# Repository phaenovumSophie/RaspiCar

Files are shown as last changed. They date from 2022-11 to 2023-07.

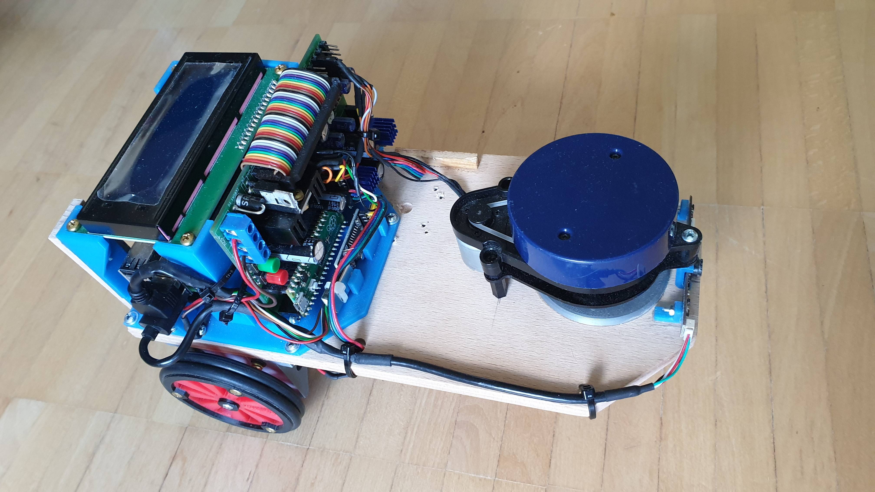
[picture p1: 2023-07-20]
RaspiCar_v2.jpg

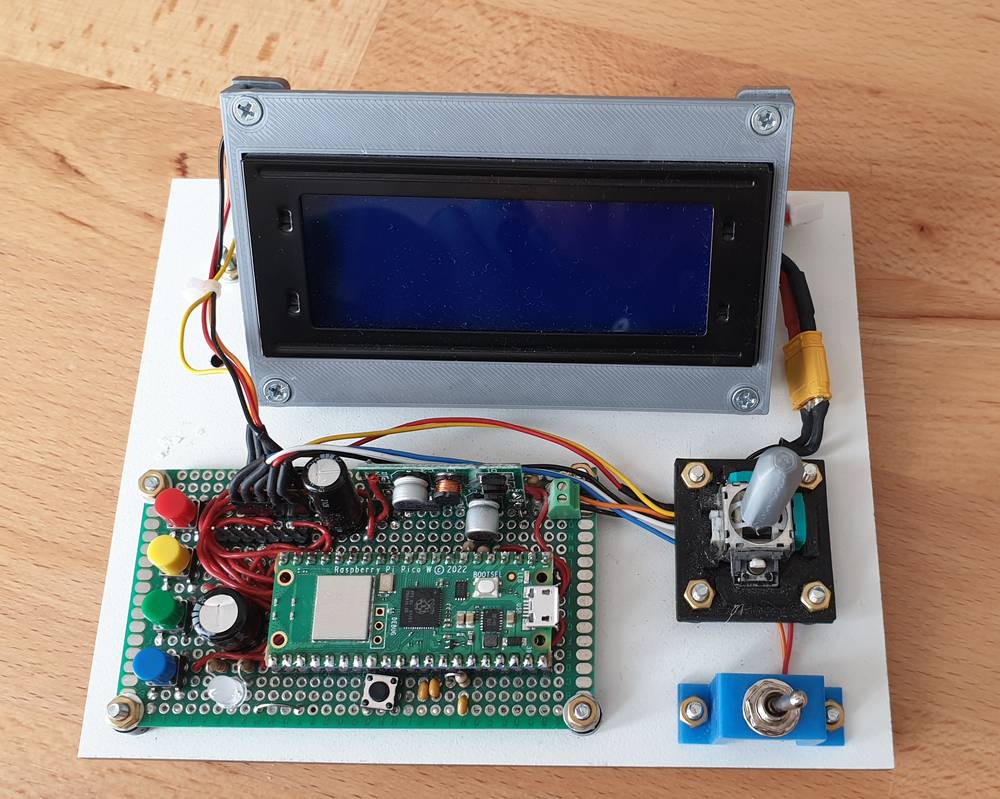
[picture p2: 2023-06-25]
RaspiCar-Controller/Circuit/Controller-Foto.jpg

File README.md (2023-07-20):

# RaspiCar
A model car equipped with a Raspberry Pi, intended for experimenting with tools and algorithms for autonomous navigation

This is a simple platform for experimenting. At this stage clearly work in progress ...

The car is based on two stepper motors for the left and right driving wheel. In addition there is a free spinning wheel in the front. Driving direction is controlled by different speed settings for the motors. The car is capable of turning on the spot. Power is provided a by a LiPo battery of 3 cells.

Raspberry Pi:
=============
The Raspberry Pi provides navigation and overall management of the car. The navigations is based on the various sensors. The software is written primarily in Python. Prototype software is avaiable to support ultrasonic sensors, LiDAR, camera and a NRF24 module for remote control. There are also experiments with machine learning alogrithms (SciKit Learn). More to be developed and to follow.

Python files:
- io_ctrl.py - This module defines the I/Os for the Raspberry Pi and a tool to send commands to the motor driver via a serial interface
- much more to come ...

Motor Driver:
=============
In addition to the Raspberry Pi, there is a board comprising a 5V step down converter, a rp2040 microcontroller, a LCD and adapters for various devices such as LiDAR, distance sensors and more. The rp2040 generates the step and direction signals for the stepper motors, with this releasing the real time workload from the Raspberry Pi. The rp2040 interfaces with the Raspberry Pi via a serial interface running at115200 baud. The rp2040 also takes care of power management by raising a shutdown signal in case the battery voltage is running low. The software for the rp2040 is based on Arduino/C++

Arduino files for the motor driver:
- rp2040_motor_driver.ino: main program
- motors.cpp, motors.h: class to run the stepper motors
- display.cpp, display.h: class to run the display
- battery.cpp, battery.h: class to provide battery and power management

List of motor commands:
The Raspberry Pi sends commands via the serial interface and receives responses. This can easily by tested via a standard terminal tool (e.g. PUTTY).
- ME0,0 / ME1,1  - disables or enables motor A and B
- MP0,0 / MP1,1  - switches motor A and B on or off
- MD0,0 / MD1,1  - sets the direction of the motor (1 -> forward, 0 -> backward)
- MR<l>,<r> - sets the speed of the motors in rounds per minute. The range is 0 to 1500. Example: "MR200,500"
- DC - clears the display (title and message)
- DT - prints a title of up to 0 characters on line 1 of the display (maximum 20 characters)
- DM - prints a message of up to 40 character on line 2 and 3 of the display
- BV - returns the current battery voltage
- BS - returns the battery voltage and the system status, separated by comma 

List of system status:
  - 0 - STATUS_OK                   'OK' - all fine
  - 1 - STATUS_BAT_LOW              'BL' - Battery low, voltage below 10.5V
  - 2 - STATUS_BAT_SHUTDOWN         'BS' - Battery very low, shutdown requested due to low power, waiting for Raspi to respond
  - 3 - STATUS_BAT_EXTERNAL         'BE  - System running on 5V external power
  - 4 - STATUS_SHUTDOWN_REQUESTED   'SR' - Shutdwon requested by user, waiting for Raspi to respond
  - 5 - STATUS_SHUTDOWN_ACTIVE      'SX' - Shutdown in progress, power will be shut in less than 10 secs

SLW October 2022

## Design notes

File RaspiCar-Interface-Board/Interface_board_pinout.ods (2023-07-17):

Raspi Pin | Raspi GPIO | Function | Connector | Pin
2 | - | +5V Power | J8 Raspi I2C | 2
3 | 02 | I2C SDA | J8 Raspi I2C | 3
4 | - | +5V Power | J8 Raspi I2C | 2
5 | 03 | I2C SCL | J8 Raspi I2C | 4
6 | - | GND | - | -
9 | - | GND | - | -
10 | 15 | Raspi RxD | J6 LiDAR | 3
14 | - | GND | - | -
17 | 3.3V Out | SPI Vcc | J5 Raspi SPI | 2
19 | 10 | Raspi MOSI | J5 Raspi SPI | 4
20 | - | GND | - | -
21 | 09 | Raspi MISO | J5 Raspi SPI | 5
23 | 11 | Raspi SCLK | J5 Raspi SPI | 3
24 | 08 | Raspi CE | J5 Raspi SPI | 6
25 | - | GND | - | -
29 | 05 | Raspi IN | Pico GP2 | 4
30 | - | GND | - | -
31 | 06 | Dual LED red | - | -
33 | '13 | Dual LED green | - | -
34 | - | GND | - | -
35 | 19 | Raspi OUT | Pico GP3 | 5
37 | 26 | LED green | - | -
39 | - | GND | - | -
40 | '21 | LiDAR Power | J6 LiDAR | 2

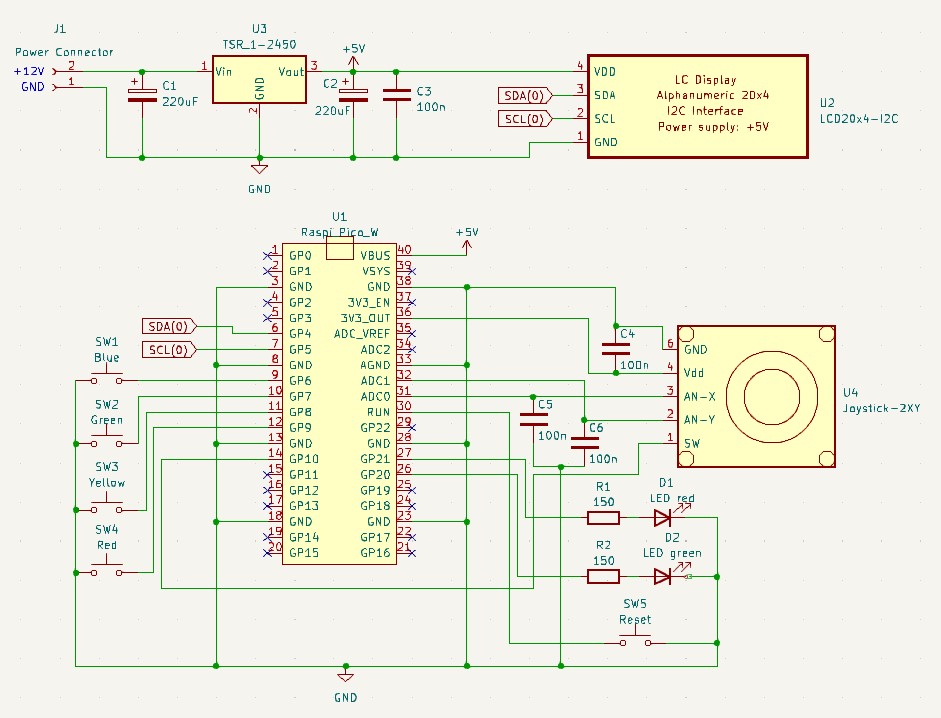
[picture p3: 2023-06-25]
RaspiCar-Controller/Circuit/Schaltplan.jpg

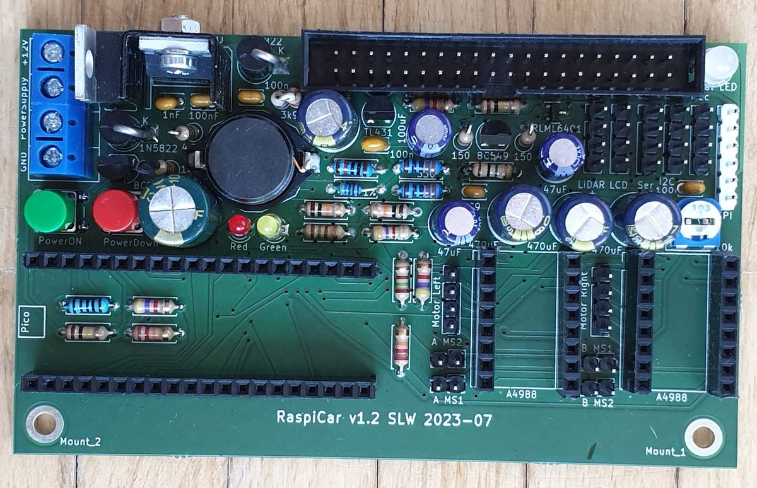
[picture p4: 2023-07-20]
RaspiCar-Interface-Board/Foto.jpg

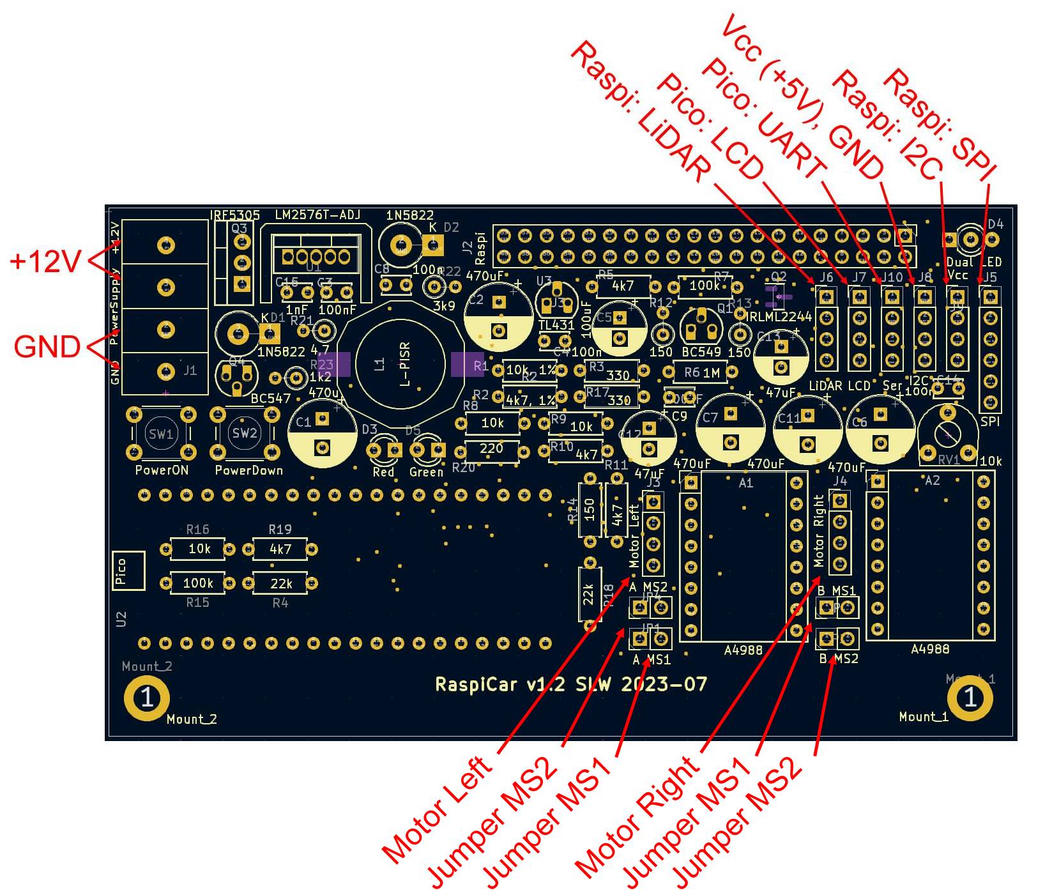
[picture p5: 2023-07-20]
RaspiCar-Interface-Board/RaspiCar-PCB-v1.2.jpg

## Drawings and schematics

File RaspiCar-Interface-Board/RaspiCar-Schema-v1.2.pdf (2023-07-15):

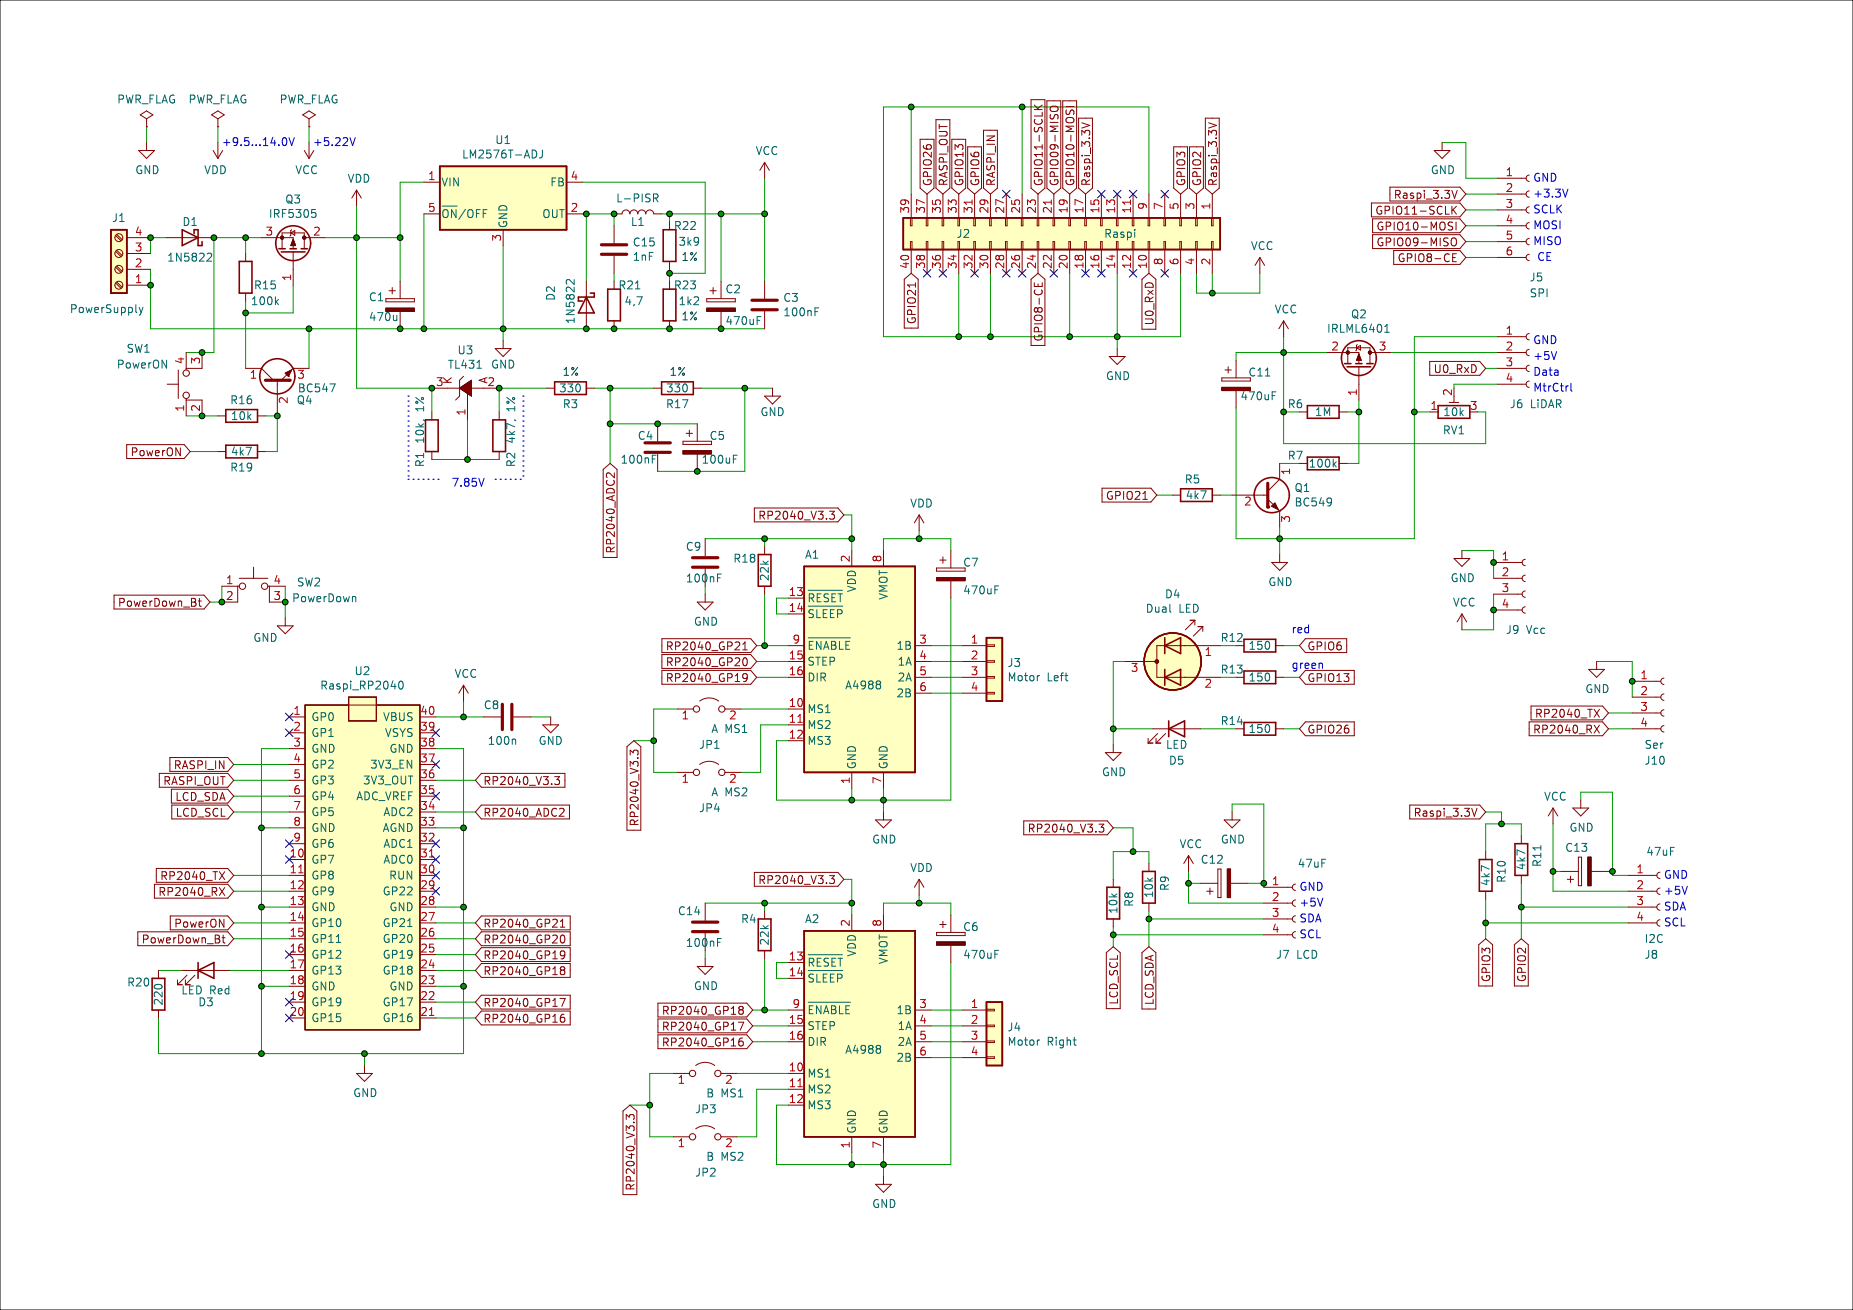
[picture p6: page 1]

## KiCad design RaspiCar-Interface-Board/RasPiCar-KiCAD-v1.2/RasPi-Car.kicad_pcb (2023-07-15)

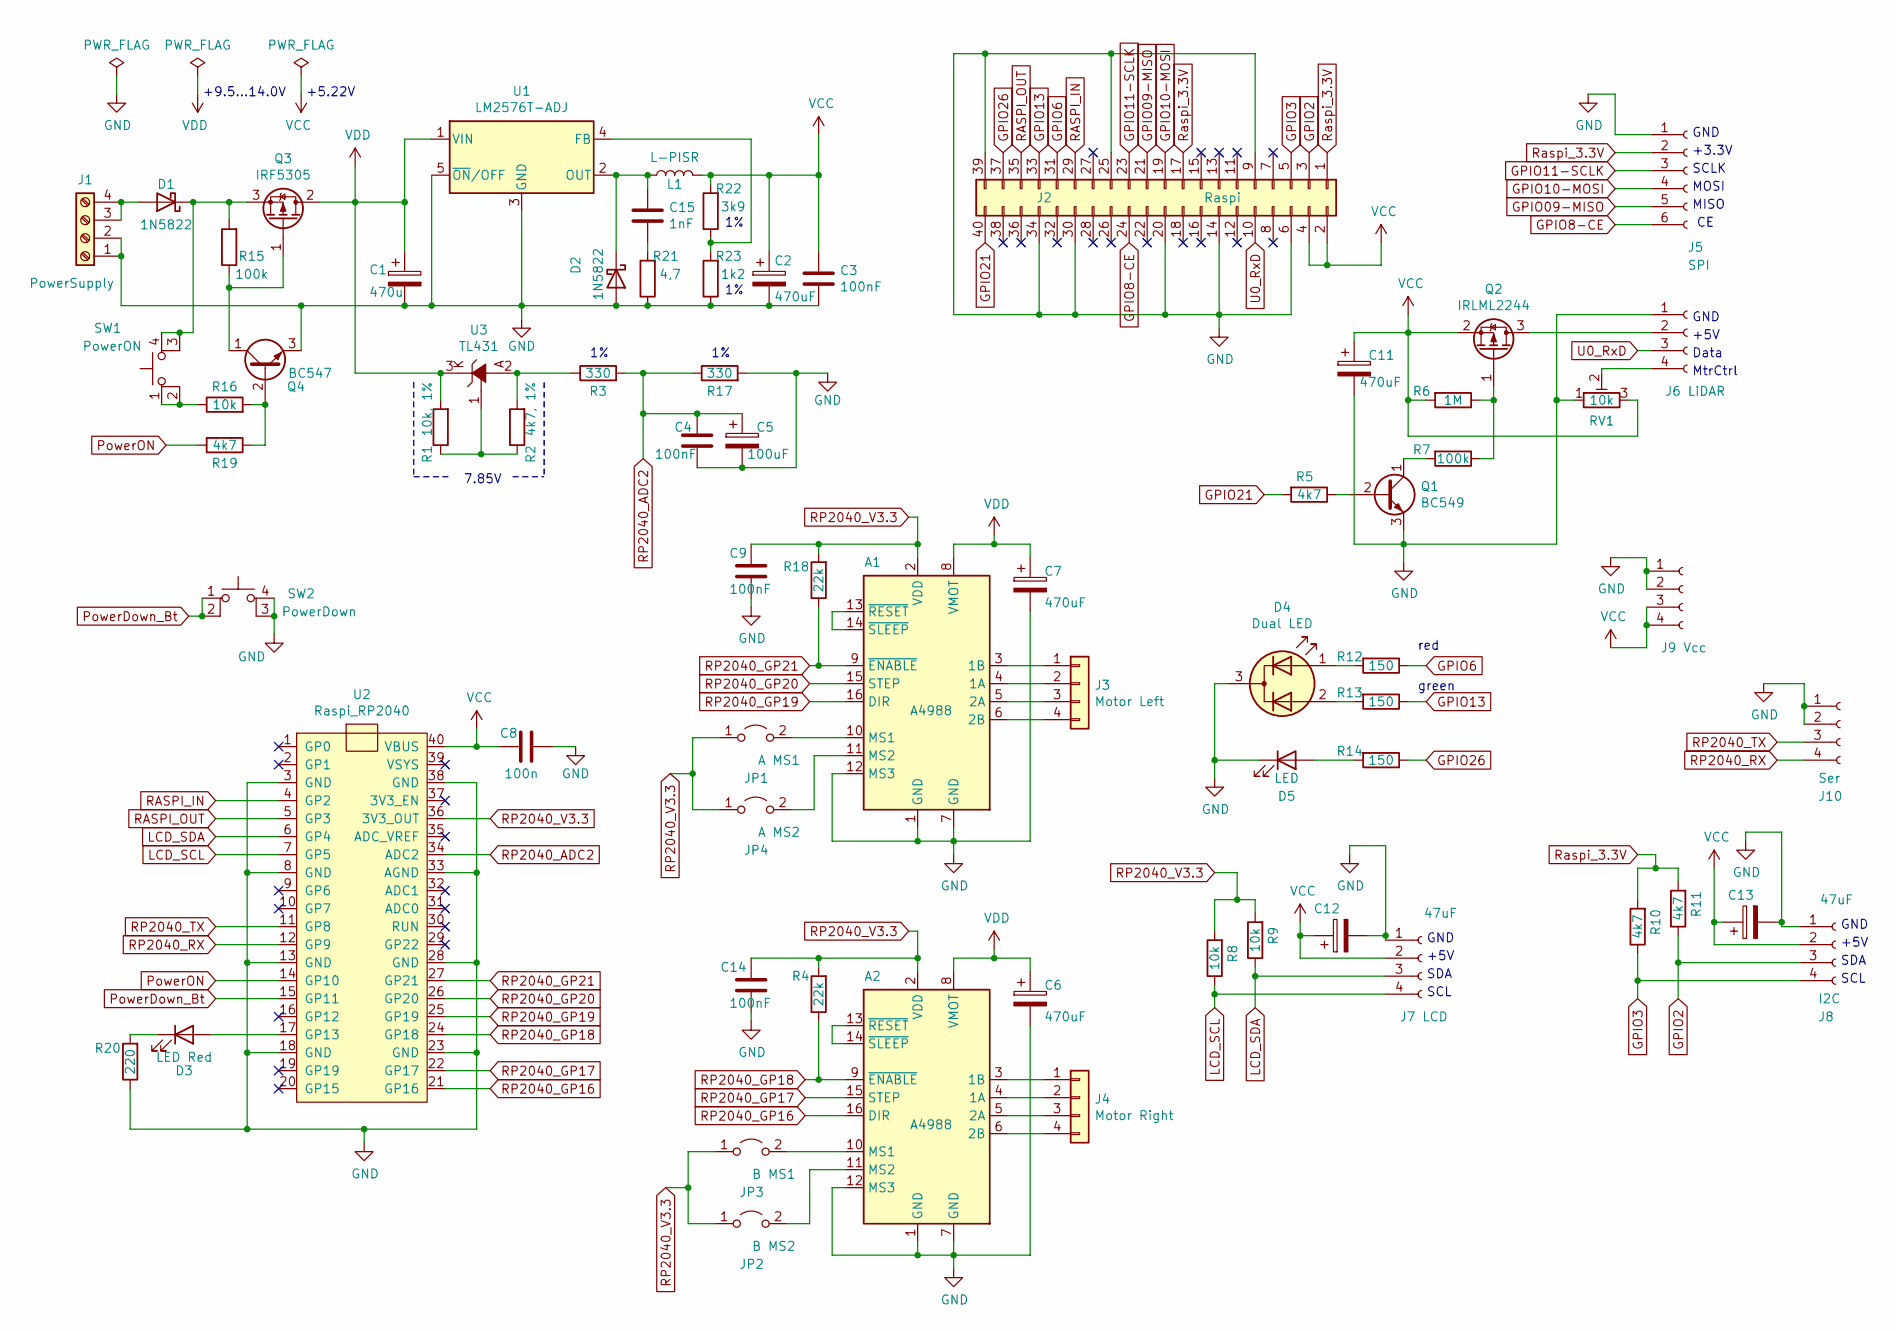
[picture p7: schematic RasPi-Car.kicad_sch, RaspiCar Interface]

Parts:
A1, A2: A4988; Pololu_Breakout-16_15.2x20.3mm
C1: 470u; CP_Radial_D8.0mm_P3.50mm
C2, C6, C7, C11: 470uF; CP_Radial_D8.0mm_P3.50mm
C3, C4, C9, C14: 100nF; C_Disc_D3.4mm_W2.1mm_P2.50mm
C5: 100uF; CP_Radial_D6.3mm_P2.50mm
C8: 100n; C_Disc_D3.4mm_W2.1mm_P2.50mm
C12, C13: 47uF; CP_Radial_D6.3mm_P2.50mm
C15: 1nF; C_Disc_D3.4mm_W2.1mm_P2.50mm
D1, D2: 1N5822; D_DO-201AE_P3.81mm_Vertical_KathodeUp
D3: LED Red; LED_D3.0mm
D4: Dual LED; LED_D3.0mm-3-center-kathode
D5: LED; LED_D3.0mm
J1: PowerSupply; ScrewTerminal_1x4
J2: Raspi; PinHeader_2x20_P2.54mm_Vertical
J3: Motor Left; PinHeader_1x04_P2.54mm_Vertical
J4: Motor Right; PinHeader_1x04_P2.54mm_Vertical
J5: SPI; PinHeader_1x06_P2.54mm_Vertical
J6: LiDAR; PinHeader_1x04_P2.54mm_Vertical
J7: LCD; PinHeader_1x04_P2.54mm_Vertical
J8: I2C; PinHeader_1x04_P2.54mm_Vertical
J9: Vcc; PinHeader_1x04_P2.54mm_Vertical
J10: Ser; PinHeader_1x04_P2.54mm_Vertical
JP1: A MS1; PinHeader_1x02_P2.54mm_Vertical
JP2: B MS2; PinHeader_1x02_P2.54mm_Vertical
JP3: B MS1; PinHeader_1x02_P2.54mm_Vertical
JP4: A MS2; PinHeader_1x02_P2.54mm_Vertical
L1: L-PISR; L-PISR-100
Q1: BC549; TO-92_HandSolder
Q2: IRLML2244; SOT-23
Q3: IRF5305; TO-220-3_Vertical
Q4: BC547; TO-92_HandSolder
R1: 10k, 1%; R_Axial_DIN0207_L6.3mm_D2.5mm_P7.62mm_Horizontal
R2: 4k7, 1%; R_Axial_DIN0207_L6.3mm_D2.5mm_P7.62mm_Horizontal
R3, R17: 330; R_Axial_DIN0207_L6.3mm_D2.5mm_P7.62mm_Horizontal
R4, R18: 22k; R_Axial_DIN0207_L6.3mm_D2.5mm_P7.62mm_Horizontal
R5, R10, R11, R19: 4k7; R_Axial_DIN0207_L6.3mm_D2.5mm_P7.62mm_Horizontal
R6: 1M; R_Axial_DIN0207_L6.3mm_D2.5mm_P7.62mm_Horizontal
R7, R15: 100k; R_Axial_DIN0207_L6.3mm_D2.5mm_P7.62mm_Horizontal
R8, R9, R16: 10k; R_Axial_DIN0207_L6.3mm_D2.5mm_P7.62mm_Horizontal
R12, R13: 150; R_Axial_DIN0207_L6.3mm_D2.5mm_P2.54mm_Vertical
R14: 150; R_Axial_DIN0207_L6.3mm_D2.5mm_P7.62mm_Horizontal
R20: 220; R_Axial_DIN0207_L6.3mm_D2.5mm_P7.62mm_Horizontal
R21: 4,7; R_Axial_DIN0207_L6.3mm_D2.5mm_P2.54mm_Vertical
R22: 3k9; R_Axial_DIN0207_L6.3mm_D2.5mm_P2.54mm_Vertical
R23: 1k2; R_Axial_DIN0207_L6.3mm_D2.5mm_P2.54mm_Vertical
RV1: 10k; R-Trim_horizontal
SW1: PowerON; SW_PUSH_6mm_H5mm
SW2: PowerDown; SW_PUSH_6mm_H5mm
U1: LM2576T-ADJ; TO-220-5_Vertical_tiny_heatsink
U2: Raspi_RP2040
U3: TL431; TO-92_HandSolder

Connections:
GND: A1.1 (GND), A1.7 (GND), A1.12 (MS3), A2.1 (GND), A2.7 (GND), A2.12 (MS3), C1.2, C2.2, C3.2, C4.1, C5.2, C6.2, C7.2, C8.1, C9.2, C11.2, C12.2, C13.2, C14.2, D2.2 (A), D4.3 (K), D5.1 (K), J1.1, J1.2, J2.6, J2.9, J2.14, J2.20, J2.25, J2.30, J2.34, J2.39, J5.1, J6.1, J7.1, J8.1, J9.1, J9.2, J10.1, J10.2, Q1.3 (E), Q4.3 (E), R17.2, R20.1, R21.1, R23.1, RV1.1, SW2.3 (K), SW2.4 (A), U1.3 (GND), U1.5 (~ON/OFF), U2.3 (GND), U2.8 (GND), U2.13 (GND), U2.18 (GND), U2.23 (GND), U2.28 (GND), U2.33 (AGND), U2.38 (GND)
GPIO2: J2.3, J8.3, R11.1
GPIO3: J2.5, J8.4, R10.1
GPIO6: J2.31, R12.1
GPIO8-CE: J2.24, J5.6
GPIO09-MISO: J2.21, J5.5
GPIO10-MOSI: J2.19, J5.4
GPIO11-SCLK: J2.23, J5.3
GPIO13: J2.33, R13.1
GPIO21: J2.40, R5.2
GPIO26: J2.37, R14.1
LCD_SCL: J7.4, R8.1, U2.7 (GP5)
LCD_SDA: J7.3, R9.1, U2.6 (GP4)
unnamed: A1.4 (1A), J3.2
unnamed: A1.3 (1B), J3.1
unnamed: A1.5 (2A), J3.3
unnamed: A1.6 (2B), J3.4
unnamed: A1.10 (MS1), JP1.2 (B)
unnamed: A1.11 (MS2), JP4.2 (B)
unnamed: A1.13 (~RESET), A1.14 (~SLEEP)
unnamed: A2.4 (1A), J4.2
unnamed: A2.3 (1B), J4.1
unnamed: A2.5 (2A), J4.3
unnamed: A2.6 (2B), J4.4
unnamed: A2.10 (MS1), JP3.2 (B)
unnamed: A2.11 (MS2), JP2.2 (B)
unnamed: A2.13 (~RESET), A2.14 (~SLEEP)
unnamed: C15.2, R21.2
unnamed: D1.2 (A), J1.3, J1.4
unnamed: D1.1 (K), Q3.3 (S), R15.2, SW1.3 (K), SW1.4 (A)
unnamed: C15.1, D2.1 (K), L1.1, U1.2 (OUT)
unnamed: D3.2 (A), U2.17 (GP13)
unnamed: D3.1 (K), R20.2
unnamed: D4.1 (A1), R12.2
unnamed: D4.2 (A2), R13.2
unnamed: D5.2 (A), R14.2
unnamed: J6.2, Q2.3 (D)
unnamed: J6.4, RV1.2
unnamed: Q1.2 (B), R5.1
unnamed: Q1.1 (C), R7.2
unnamed: Q2.1 (G), R6.1, R7.1
unnamed: Q3.1 (G), Q4.1 (C), R15.1
unnamed: Q4.2 (B), R16.2, R19.1
unnamed: R16.1, SW1.1, SW1.2
unnamed: R22.1, R23.2, U1.4 (FB)
unnamed: R2.2, R3.1, U3.2 (A)
unnamed: R1.1, R2.1, U3.1 (R)
PowerDown_Bt: SW2.1, SW2.2, U2.15 (GP11)
PowerON: R19.2, U2.14 (GP10)
RASPI_IN: J2.29, U2.4 (GP2)
RASPI_OUT: J2.35, U2.5 (GP3)
RP2040_ADC2: C4.2, C5.1, R3.2, R17.1, U2.34 (ADC2)
RP2040_GP16: A2.16 (DIR), U2.21 (GP16)
RP2040_GP17: A2.15 (STEP), U2.22 (GP17)
RP2040_GP18: A2.9 (~ENABLE), R4.1, U2.24 (GP18)
RP2040_GP19: A1.16 (DIR), U2.25 (GP19)
RP2040_GP20: A1.15 (STEP), U2.26 (GP20)
RP2040_GP21: A1.9 (~ENABLE), R18.1, U2.27 (GP21)
RP2040_RX: J10.4, U2.12 (GP9)
RP2040_TX: J10.3, U2.11 (GP8)
RP2040_V3.3: A1.2 (VDD), A2.2 (VDD), C9.1, C14.1, JP1.1 (A), JP2.1 (A), JP3.1 (A), JP4.1 (A), R4.2, R8.2, R9.2, R18.2, U2.36 (3V3_OUT)
Raspi_3.3V: J2.1, J2.17, J5.2, R10.2, R11.2
U0_RxD: J2.10, J6.3
VCC: C2.1, C3.1, C8.2, C11.1, C12.1, C13.1, J2.2, J2.4, J7.2, J8.2, J9.3, J9.4, L1.2, Q2.2 (S), R6.2, R22.2, RV1.3, U2.40 (VBUS)
VDD: A1.8 (VMOT), A2.8 (VMOT), C1.1, C6.1, C7.1, Q3.2 (D), R1.2, U1.1 (VIN), U3.3 (K)

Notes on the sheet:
SCL
+9.5...14.0V
+5V
7.85V
SDA
MtrCtrl
Data
SCLK
red
MISO
GND
+5.22V
+3.3V
MOSI
green

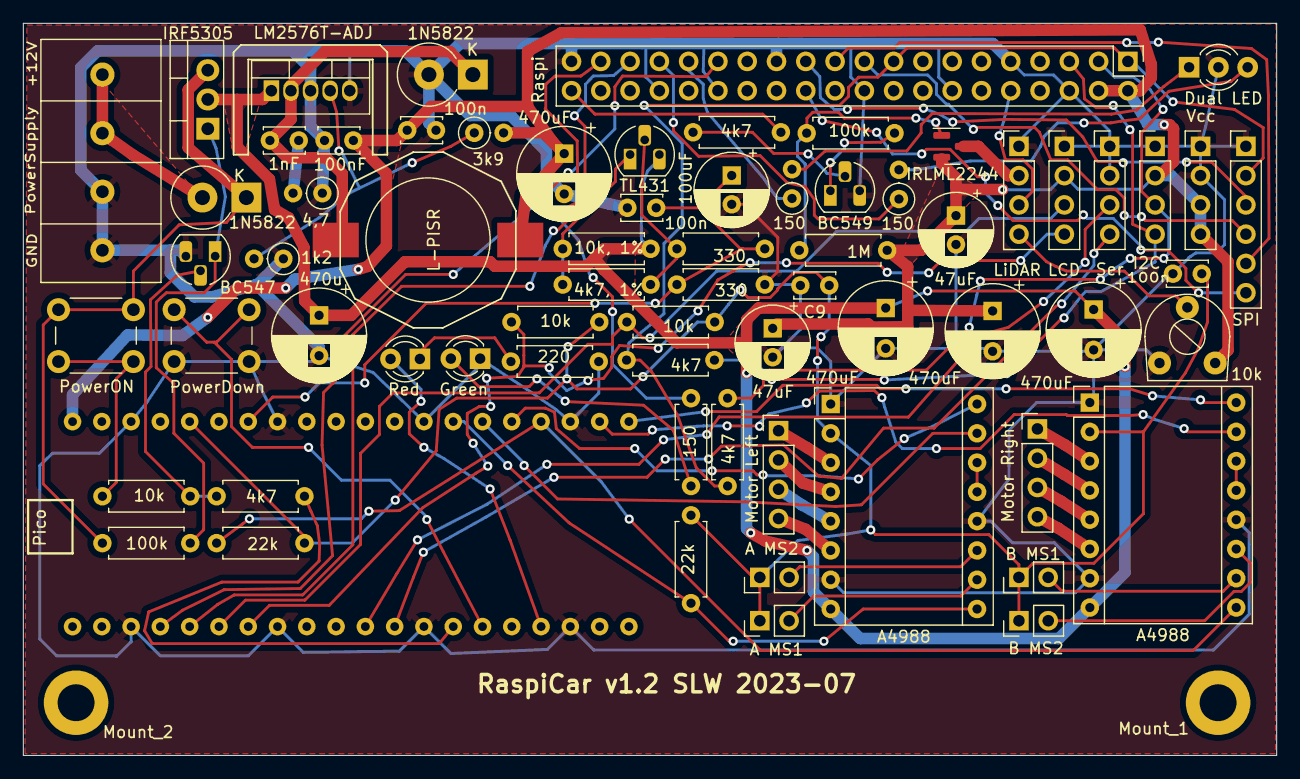
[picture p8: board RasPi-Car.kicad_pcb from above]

Board: 2 copper layers, 108.7 x 63.5 mm, 71 parts (0 on the bottom side), 65 nets.

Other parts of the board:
Mount_1: Mount_1; MountingHole_3.2mm_M3_DIN965_Pad
Mount_2: Mount_2; MountingHole_3.2mm_M3_DIN965_Pad

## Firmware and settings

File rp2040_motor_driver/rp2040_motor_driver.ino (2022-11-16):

/*
 * rp2040 Motor Driver (RaspiCar)
 * This module is part of the phaenovum RaspiCar project. 
 * It provides driver function for two stepper motors. Beyond that, it serves 
 * as power and battery manager. Finally, it includes a LCD display to shows 
 * status information and simplify debugging. It uses a seruial interface
 * (fixed baud rate at 115200) for communication with the Raspberry Pi. 
 * 
 * SLW - October 2022
 */

#include "display.h"
#include "motors.h"
#include "battery.h"
#include "util.h"

#define BUF_SIZE 40

// Pins
#define SERIAL_TX         8      // serial interface to Raspberry Pi
#define SERIAL_RX         9
#define RASPI_IN          2      // reserve: additional GPIO to RaspiPi 
#define RASPI_OUT         3      // reserve: additional GPIO to RaspiPi 

// Decode input from serial interface
#define VALID_LIMIT 999999

// Global variables
LCD_Display display;
Motors motors;
Battery bat;
char buf[BUF_SIZE];
int buf_pnt=0;
int i = 0;
volatile uint8_t job_flags = 0b00000000;
int power_down_bt_status = 0;


//-------------------------------------------------------------------------
// Adds a char from the serial interface to the input buffer. 
// Returns false, unless a end-of-line character is detected.
bool add_to_buffer(char c) {
  switch ((uint8_t) c) {
    case 13:   // carriage return
    case 10:   // line feed
      buf[buf_pnt] = '\0';
      buf_pnt = 0;
      return true;
    case 8:    // backspace
      buf[buf_pnt] = '\0';
      if (buf_pnt > 0) buf_pnt -= 1;
      break;
    default:     // all other chars
      buf[buf_pnt] = c;
      if (buf_pnt < BUF_SIZE - 1) 
      ++buf_pnt;
  }
  return false;
}

//-------------------------------------------------------------------------
// get_int
// Extracts an integer from the input buffer. 
// Moves the pointer to the next position after the integer
int32_t get_int(uint8_t *pnt) {
  int32_t result = 0;
  bool negative_flag = false, done = false, valid = false;

  while (buf[*pnt] == ' ') *pnt += 1;     // skip leading blanks
  
  while (!done) {
    if (buf[*pnt] == '+') {
      negative_flag = false;
    } else if (buf[*pnt] == '-') {
      negative_flag = true;
    } else if ((buf[*pnt] >= '0') && (buf[*pnt] <= '9')) {
      result = result * 10;
      result += buf[*pnt] - '0';
      valid = true;
    } else {
      done = true;
    }
    if (buf[*pnt] != '\0')      // don't progress beyond end of string
      *pnt += 1;
  }
  if (!valid) {
    result = VALID_LIMIT;
  } else if (negative_flag) {
    result = -result;
  }
  return result;
}

//-------------------------------------------------------------------------
void decode_bat_command(uint8_t pnt) {
  char local_buf[16];
  bool okay = true;
  
  switch (buf[pnt]) {
    case 'v':               // get battery voltage
    case 'V':
      itoaf(bat.get_voltage(), local_buf, 4, 2, false);
      uart_puts(uart1, local_buf); 
      break;

    case 's':               // get battery status
    case 'S':
      bat.get_full_status(local_buf);
      uart_puts(uart1, local_buf);
      break;

    case 'x':
    case 'X':
      display.print_msg("Shutting down");
      bat.start_shutdown();
      uart_puts(uart1, "OK");
      break;
 
    default:
      okay = false;
  }
  if (!okay) {
      uart_puts(uart1, "Battery command not recognized: ");
      uart_puts(uart1, buf);
  }
  uart_puts(uart1, "\r\n");
}

//-------------------------------------------------------------------------
void decode_display_command(uint8_t pnt) {
  bool okay = true;
  
  switch (buf[pnt]) {
    case 'c':           // clear display
    case 'C':
      display.clear();
      break;
      
    case 't':           // print title
    case 'T':
      display.print_title(buf+2);
      break;
      
    case 'm':           // print message
    case 'M':
      display.print_msg(buf+2);
      break;
      
    default:
      okay = false;
  }
  if (okay) {
    uart_puts(uart1, "OK");
  } else {
      uart_puts(uart1, "Display command not recognized: ");
      uart_puts(uart1, buf);
  }
  uart_puts(uart1, "\r\n");
}

//-------------------------------------------------------------------------
void decode_motor_command(uint8_t pnt) {
  int32_t a, b;
  bool okay = true;

  switch (buf[pnt]) {
    case 'd':
    case 'D':                                 // dir
      pnt += 1;
      a = get_int(&pnt);    
      b = get_int(&pnt);
      if (a < VALID_LIMIT) {
        motors.set_a_dir(a > 0);
      }
      if (b < VALID_LIMIT) {
        motors.set_b_dir(b > 0);
      }     
      break;
    
    case 'e':
    case 'E':                                 // enable
      pnt += 1;
      a = get_int(&pnt);    
      b = get_int(&pnt);
      if (a < VALID_LIMIT) {
        motors.set_a_enable(a > 0);
        display.mot_a_enabled(motors.get_a_enabled());
      }
      if (b < VALID_LIMIT) {
        motors.set_b_enable(b > 0);
        display.mot_b_enabled(motors.get_b_enabled());
      }     
      break;
      
    case 'p':
    case 'P':                                 // power
      pnt += 1;
      a = get_int(&pnt);    
      b = get_int(&pnt);
      if (a < VALID_LIMIT) {
        motors.set_a_power(a > 0);
        display.mot_a_power(motors.get_a_power());
      }
      if (b < VALID_LIMIT) {
        motors.set_b_power(b > 0);
        display.mot_b_power(motors.get_b_power());
      }     
      break;

    /*
    case 't':                             // set cycle time
    case 'T':
      pnt += 1;
      a = get_int(&pnt);    
      b = get_int(&pnt);
      if (a < VALID_LIMIT) {
        if (a < MOT_STEP_TIME_MIN) {
          a = MOT_STEP_TIME_MIN;
          uart_puts(uart1, "Mot A: Lower limit\n\r");
        }
        else if (a > MOT_STEP_TIME_MAX) {
          a = MOT_STEP_TIME_MAX;
          uart_puts(uart1, "Mot A: Upper limit\n\r");
        }
        mot_a_step_time_target = a;  
        display.mot_a_rpm(CONVERSION_FACTOR / a);  
      }
      if (b < VALID_LIMIT) {
        if (b < MOT_STEP_TIME_MIN) {
          b = MOT_STEP_TIME_MIN;
          uart_puts(uart1, "Mot B: Lower limit\n\r");
        }
        else if (b > MOT_STEP_TIME_MAX) {
          uart_puts(uart1, "Mot B: Upper limit\n\r");
          b = MOT_STEP_TIME_MAX;
        }
        mot_b_step_time_target = b; 
        display.mot_b_rpm(CONVERSION_FACTOR / b);  
      }
      */
      break;   

    case 'r':
    case 'R':                         // set rounds per minute
      pnt += 1;
      a = get_int(&pnt);    
      b = get_int(&pnt);
      if (a < VALID_LIMIT) {
        motors.set_a_rpm(a);
        display.mot_a_rpm(motors.get_a_rpm());
        display.mot_a_enabled(motors.get_a_enabled()); 
        display.mot_a_power(motors.get_a_power());
      };
      if (b < VALID_LIMIT) {
        motors.set_b_rpm(b);
        display.mot_b_rpm(motors.get_b_rpm());
        display.mot_b_enabled(motors.get_b_enabled()); 
        display.mot_b_power(motors.get_b_power());
      };
      break;
      
    default:
      okay = false;
  }
  if (okay) {
    uart_puts(uart1, "OK");
  } else {
    uart_puts(uart1, "Motor command not recognized: ");
    uart_puts(uart1, buf);
  }
  uart_puts(uart1, "\r\n");
}

//-------------------------------------------------------------------------
void decode_command(void) {
  uint8_t pnt = 0;

  while (buf[pnt] == ' ') pnt += 1;     // skip leading blanks
  if (strlen(buf+pnt) == 0) {
    uart_puts(uart1, "\r\n");
    return;
  }
  
  switch (buf[pnt]) {
    case 'b':
    case 'B':
      decode_bat_command(pnt+1);
      break;
    case 'd':
    case 'D':
      decode_display_command(pnt+1);
      break;
    case 'm':
    case 'M':
      decode_motor_command(pnt+1);
      break;
    default:
      uart_puts(uart1, "Not recognized: ");
      uart_puts(uart1, buf);
      uart_puts(uart1, "\r\n");
  }  
}    

//-------------------------------------------------------------------------
void setup() {
  // initialize power management
  pinMode(POWER_ON, OUTPUT);
  digitalWrite(POWER_ON, HIGH);
  pinMode(POWER_DOWN_BT, INPUT_PULLUP);
  pinMode(RASPI_IN, OUTPUT);
  pinMode(RASPI_OUT, INPUT);

  Serial.begin(115200);

  // initialize serial interface to RaspPi
  gpio_set_function(SERIAL_TX, GPIO_FUNC_UART);   // TX 
  gpio_set_function(SERIAL_RX, GPIO_FUNC_UART);   // RX
  uart_init(uart1, 115200);

  // start motors
  motors.init();

  // start battery management
  bat.init();

  // initialize reserve GPIOs to and from Raspi
  pinMode(RASPI_OUT, INPUT);
  pinMode(RASPI_IN, OUTPUT);
  digitalWrite(RASPI_IN, LOW);

  // start display
  display.init();

  delay(100);
}

long cnt=0;

//-------------------------------------------------------------------------
void loop() {
  char local_buf[16];
  
  if (uart_is_readable(uart1)) {
    if (add_to_buffer(uart_getc(uart1)) == true) {
      decode_command();
    }
  }

  if (job_flags & (1 << JF_REFRESH_BAT_VOLTAGE)) {
    job_flags &= ~(1 << JF_REFRESH_BAT_VOLTAGE);
    if (bat.run_adc()) { 
      display.show_voltage(bat.get_voltage());
    if (bat.get_status() == STATUS_BAT_SHUTDOWN) 
      bat.request_bat_shutdown();
    }
    motors.check_step_time_a();
    motors.check_step_time_b();
  }
}

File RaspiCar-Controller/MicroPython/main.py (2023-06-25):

"""
RaspiCar Controller via socket UDP protocol
SLW - June-2023
"""

import time
import network
import socket
from machine import I2C, Pin, ADC, Timer
import os
from lcd_i2c import LCD

__version__ = '20230624'

#---------------------------------------------------------------------------    
def lcd_print(txt):
    lcd.set_cursor(col=0, row=0)
    lcd.print(lcd_rows[lcd_rows_pnt[1]])
    lcd.set_cursor(col=0, row=1)
    lcd.print(lcd_rows[lcd_rows_pnt[2]])
    lcd.set_cursor(col=0, row=2)
    lcd.print(lcd_rows[lcd_rows_pnt[3]])
    l = len(txt)
    if l > 20:
        lcd_rows[lcd_rows_pnt[0]] = txt[:20]
    else:
        lcd_rows[lcd_rows_pnt[0]] = txt + (20 - l) * ' '
    lcd.set_cursor(0, 3)
    lcd.print(lcd_rows[lcd_rows_pnt[0]])
    x = lcd_rows_pnt[0]
    lcd_rows_pnt[0] = lcd_rows_pnt[1]
    lcd_rows_pnt[1] = lcd_rows_pnt[2]
    lcd_rows_pnt[2] = lcd_rows_pnt[3]
    lcd_rows_pnt[3] = x
    
#---------------------------------------------------------------------------    
def read_config(config_file):
    # Read config file
    files = os.listdir()
    if config_file not in os.listdir():
        cfg = open(config_file, "w")
        cfg.write("RaspiCar Ctrl config file\n")
        cfg.write("port : 12000\n")
        cfg.write("lcd_timeout : 30\n")
        cfg.close()

    cfg = open(config_file)
    lines = cfg.readlines()
    cfg.close()

    config = {}
    for l in lines[1:]:
        key, value = l.split(':')
        config[key.strip(' ')] = value[:-1].strip(' ')
    return config


#---------------------------------------------------------------------------    
def write_config(config_file):
    # Write config file
    cfg = open(config_file, "w")
    cfg.write("RaspiCar Ctrl config file\n")
    for key, value in config.items():
        cfg.write(key + ' : ' + value + '\n')
    print("Config file saved!")
    cfg.close()


#---------------------------------------------------------------------------    
def try_connection(ssid, password, static_ip):
    """ Tries a connection on the given credentials.
    In case of success it returns True and ip address.
    In case of failure it returns False and 0.
    Requires an active wlan_node  """

    lcd_print("SSID: " + ssid)
    led_red.value(1)
    led_green.value(0)
    ssid_bytes = ssid.encode('UTF-8')  
    connected = False

    if static_ip != '<none>':
        last_dot = static_ip.rfind('.')
        gateway_ip = static_ip[:static_ip.rfind('.')] + '.1'
        lcd_print("Requesting static IP")
        wlan_node.ifconfig((static_ip, '255.255.255.0', gateway_ip, gateway_ip))

    for number_of_attempts in range(3):
        wlan_node.connect(ssid_bytes, password.encode('UTF-8'))
        for i in range(10):
            led_green.toggle()
            led_red.toggle()
            if wlan_node.isconnected():
                connected = True
                break
            time.sleep(0.5)    
        if connected:
            break
    
    if connected:
        led_red.value(0)
        led_green.value(1)
        time.sleep(0.5)
        server_ip_addr = wlan_node.ifconfig()[0]
        lcd_print("IP: " + server_ip_addr)
        return True, server_ip_addr
    else:
        lcd_print("failed ...")
        led_red.value(1)
        led_green.value(0)
        return False, '0'
    
#---------------------------------------------------------------------------
def connect_to_wlan(ssid_file):

    # Reading ssids from file
    try:
        with open(ssid_file, "r") as f:
            lines = f.readlines()
    except:
        print("Could not open " + ssid_file + "!")
        print("Closing")
        return None
    
    ssids = {}
    for l in lines:
        if len(l) > 2:
            data = l.split(',')
            if len(data) == 2:
                s, p = l.split(',')
                s, p, static_ip = s.strip(' '), p[:-2].strip(' '), '<none>'
                ssids[s] = (p, static_ip)
            elif len(data) == 3:
                s, p, static_ip = l.split(',')
                s, p, static_ip = s.strip(' '), p.strip(' '), static_ip[:-2].strip(' ')
                ssids[s] = (p, static_ip)
            else:
                print("SSID data error - can't decode line " + l)
                print("Program stopped")
                while True:
                    pass

    # Scanning network
    all_nets = [(net[0].decode('UTF-8'), net[3]) for net in wlan_node.scan()]
    # Limiting to know networks
    all_nets = [net for net in all_nets if net[0] in ssids.keys()]
    # Adding password and static IP
    all_nets = [(net[0], net[1], ssids[net[0]][0], ssids[net[0]][1]) for net in all_nets]
    
    # Finding suitable network and trying to connect
    server_ip_addr = '0.0.0.0'
    if len(all_nets) == 0:
        lcd_print("No network ...")
        while True:
            pass
    else:
        # Sort networks by signal strength
        all_nets = sorted(all_nets, key=lambda x: x[1], reverse=True)
        for net in all_nets:
            success, server_ip_addr = try_connection(net[0], net[2], net[3])
            if success:
                break

    return server_ip_addr


#---------------------------------------------------------------------------
def timer_interrupt(tim):
    """ Manage lcd backlight """
    global lcd_light_cnt, lcd_light_is_on

    if bt_blue.value() == 0:
        lcd_light_cnt = lcd_timeout

    if lcd_light_cnt == lcd_timeout:
        if not lcd_light_is_on:
            lcd.backlight()
            lcd_light_is_on = True
    elif lcd_light_cnt == 0:
        if lcd_light_is_on:
            lcd.no_backlight()
            lcd_light_is_on = False
    if lcd_light_cnt >= 0:
        lcd_light_cnt -= 1
    
        
#==============================================================================

# Pin definitions
led_green = Pin(20, Pin.OUT)
led_red = Pin(21, Pin.OUT)
bt_blue = Pin(6, Pin.IN, Pin.PULL_UP)
bt_green = Pin(7, Pin.IN, Pin.PULL_UP)
bt_yellow = Pin(8, Pin.IN, Pin.PULL_UP)
bt_red = Pin(9, Pin.IN, Pin.PULL_UP)
bt_joystick = Pin(10, Pin.IN, Pin.PULL_UP)

# Global constants
config_file_name = "raspicar_ctrl.config"
ssid_file_name = "ssid.dat"
config = read_config(config_file_name)

# Global variables
lcd_rows = [20 * ' ', 20 * ' ', 20 * ' ', 20 * ' ']
lcd_rows_pnt = [0, 1, 2, 3]
lcd_timeout = int(config['lcd_timeout']) * 4
lcd_light_cnt = lcd_timeout
lcd_light_is_on = True

# Initiate network
network.country('DE')
network.hostname(config.get('hostname', 'RaspiCarCrtl'))
wlan_node = network.WLAN(network.STA_IF)
wlan_node.active(True)

# Start LC display
i2c = I2C(0, sda=Pin(4), scl=Pin(5), freq=800000)
lcd = LCD(addr=0x27, cols=20, rows=4, i2c=i2c)
lcd.begin()
lcd_print("RaspiCar " + __version__)

# Toogle LEDs
led_green.value(1)
time.sleep(0.3)
led_green.value(0)
led_red.value(1)
time.sleep(0.3)
led_red.value(0)

# Connect to network
server_ip_addr = connect_to_wlan(ssid_file_name)
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

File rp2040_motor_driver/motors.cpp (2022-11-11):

#include "motors.h"

struct repeating_timer mot_a_timer;
struct repeating_timer mot_b_timer;

//----------------------------------------------------------------------
void Motors::init(void) {
  pinMode(MOTA_PWR, OUTPUT);
  digitalWrite(MOTA_PWR, HIGH);
  pinMode(MOTA_STEP, OUTPUT);
  digitalWrite(MOTA_STEP, HIGH);
  pinMode(MOTA_DIR, OUTPUT);
  digitalWrite(MOTA_DIR, HIGH);
  pinMode(MOTB_PWR, OUTPUT);
  digitalWrite(MOTB_PWR, HIGH);
  pinMode(MOTB_STEP, OUTPUT);
  digitalWrite(MOTB_STEP, HIGH);
  pinMode(MOTB_DIR, OUTPUT);
  digitalWrite(MOTB_DIR, HIGH);
  
  add_repeating_timer_us(a_step_time, mot_a_timer_callback, NULL, &mot_a_timer);
  add_repeating_timer_us(b_step_time, mot_b_timer_callback, NULL, &mot_b_timer);
}

//----------------------------------------------------------------------
void Motors::set_a_enable(bool status) {
  a_enabled = status;
  if (!a_enabled) a_step_time_target = MOT_STEP_TIME_MAX; 
}

//----------------------------------------------------------------------
void Motors::set_b_enable(bool status) {
  b_enabled = status;
  if (!b_enabled) b_step_time_target = MOT_STEP_TIME_MAX; 
}

//----------------------------------------------------------------------
void Motors::set_a_power(bool status) {
  a_power = status;
  digitalWrite(MOTA_PWR, !status);
  if (!a_power) a_step_time_target = MOT_STEP_TIME_MAX;
}

//----------------------------------------------------------------------
void Motors::set_b_power(bool status) {
  b_power = status;
  digitalWrite(MOTB_PWR, !status);
  if (!b_power) b_step_time_target = MOT_STEP_TIME_MAX;
}

//----------------------------------------------------------------------
bool Motors::get_a_enabled(void) {
  return a_enabled;
}

//----------------------------------------------------------------------
bool Motors::get_b_enabled(void) {
  return b_enabled;
}

//----------------------------------------------------------------------
bool Motors::get_a_power(void) {
  return a_power;
}

//----------------------------------------------------------------------
bool Motors::get_b_power(void) {
  return b_power;
}

//----------------------------------------------------------------------
void Motors::set_a_dir(bool status) {
  a_dir = status;
  digitalWrite(MOTA_DIR, status);
}

//----------------------------------------------------------------------
void Motors::set_b_dir(bool status) {
  b_dir = status;
  digitalWrite(MOTB_DIR, status);
}

//----------------------------------------------------------------------
void Motors::check_step_time_a(void) {
  if (a_step_time > a_step_time_target) {   // faster
    a_step_time = calc_step_time(a_step_time, true);
    if (a_step_time < a_step_time_target) a_step_time = a_step_time_target;
    mot_a_timer.delay_us = a_step_time;
  } else if (a_step_time < a_step_time_target) {   // slower
    a_step_time = calc_step_time(a_step_time, false);
    if (a_step_time > a_step_time_target) a_step_time = a_step_time_target;
    mot_a_timer.delay_us = a_step_time;
  }
  if (a_step_time >= MOT_STEP_TIME_MAX) {
    set_a_enable(false);
  }
}

//----------------------------------------------------------------------
void Motors::check_step_time_b(void) {
  if (b_step_time > b_step_time_target) {           // faster
    b_step_time = calc_step_time(b_step_time, true);
    if (b_step_time < b_step_time_target) b_step_time = b_step_time_target;
    mot_b_timer.delay_us = b_step_time;
  } else if (b_step_time < b_step_time_target) {    // slower
    b_step_time = calc_step_time(b_step_time, false);
    if (b_step_time > b_step_time_target) b_step_time = b_step_time_target;
    mot_b_timer.delay_us = b_step_time;
  }
    if (b_step_time >= MOT_STEP_TIME_MAX) {
    set_b_enable(false);
  }
}

//-------------------------------------------------------------------------
uint32_t Motors::calc_step_time(uint32_t current_step_time, bool up) {
  uint32_t new_step_time;
  int rpm = CONVERSION_FACTOR / current_step_time;
  int new_rpm;
  
  if (up) {               // faster - reduce step_time
    new_rpm = rpm + mot_ramp;
    if (new_rpm > RPM_MAX) new_rpm = RPM_MAX;
    new_step_time = CONVERSION_FACTOR / new_rpm;
    if (new_step_time >= current_step_time) new_step_time = current_step_time - 1;  
  } else {                // slower - increase step_time
    new_rpm = rpm - mot_ramp;
    if (new_rpm < RPM_MIN) new_rpm = RPM_MIN;
    new_step_time = CONVERSION_FACTOR / new_rpm;
    if (new_step_time <= current_step_time) new_step_time = current_step_time + 1;  
  }
  return new_step_time;
}

//-------------------------------------------------------------------
void Motors::set_a_steptime(uint32_t steptime) {
  a_step_time_target = steptime;
  if (a_step_time_target < MOT_STEP_TIME_MIN)
   a_step_time_target = MOT_STEP_TIME_MIN;
  else if (a_step_time_target > MOT_STEP_TIME_MAX)
   a_step_time_target = MOT_STEP_TIME_MAX;
}

//-------------------------------------------------------------------
void Motors::set_b_steptime(uint32_t steptime) {
  b_step_time_target = steptime;
  if (b_step_time_target < MOT_STEP_TIME_MIN)
    b_step_time_target = MOT_STEP_TIME_MIN;
  else if (b_step_time_target > MOT_STEP_TIME_MAX)
    b_step_time_target = MOT_STEP_TIME_MAX;
}

//-------------------------------------------------------------------
void Motors::set_a_rpm(uint32_t rpm) {
  if (rpm == 0) {
    a_step_time_target = MOT_STEP_TIME_MAX;
  } else {
    a_step_time_target = CONVERSION_FACTOR / rpm;
    if (a_step_time_target < MOT_STEP_TIME_MIN)
      a_step_time_target = MOT_STEP_TIME_MIN;
    else if (a_step_time_target > MOT_STEP_TIME_MAX)
      a_step_time_target = MOT_STEP_TIME_MAX;
    a_enabled = true;
  }
}

//-------------------------------------------------------------------
void Motors::set_b_rpm(uint32_t rpm) {
  if (rpm == 0) {
    b_step_time_target = MOT_STEP_TIME_MAX;
  } else {
    b_step_time_target = CONVERSION_FACTOR / rpm;
    if (b_step_time_target < MOT_STEP_TIME_MIN)
      b_step_time_target = MOT_STEP_TIME_MIN;
    else if (b_step_time_target > MOT_STEP_TIME_MAX)
      b_step_time_target = MOT_STEP_TIME_MAX;
    b_enabled = true;
  }
}

//-------------------------------------------------------------------
uint32_t Motors::get_a_rpm(void) {
  if (a_step_time_target >= MOT_STEP_TIME_MAX) return 0; 
  return CONVERSION_FACTOR / a_step_time_target;
}

//-------------------------------------------------------------------
uint32_t Motors::get_b_rpm(void) {
  if (b_step_time_target >= MOT_STEP_TIME_MAX) return 0; 
  return CONVERSION_FACTOR / b_step_time_target;
}

//-------------------------------------------------------------------
bool mot_a_timer_callback(struct repeating_timer *t) {
  extern Motors motors;
  if (motors.a_enabled) {
    if (digitalRead(MOTA_STEP) == HIGH)
      digitalWrite(MOTA_STEP, LOW);
    else
      digitalWrite(MOTA_STEP, HIGH);
  }
  return true;
}
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

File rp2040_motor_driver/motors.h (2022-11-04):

#ifndef __MOTORS__
#define __MOTORS__

#include <arduino.h>

// pin definitions
#define MOTA_PWR         21
#define MOTA_STEP        20
#define MOTA_DIR         19
#define MOTB_PWR         18
#define MOTB_STEP        17
#define MOTB_DIR         16

// Motor step time
#define MOT_STEP_TIME_MAX 150000
#define MOT_STEP_TIME_MIN    100
#define CONVERSION_FACTOR 150000
#define MOT_RAMP              15
#define RPM_MAX             1500
#define RPM_MIN                1

// Function prototypes
bool mot_a_timer_callback(struct repeating_timer *t);
bool mot_b_timer_callback(struct repeating_timer *t);

class Motors {
  private:
    bool a_dir = true;
    bool b_dir = true;
	  int mot_ramp = MOT_RAMP;
	  uint32_t calc_step_time(uint32_t current_step_time, bool up);
    uint32_t a_step_time_target = MOT_STEP_TIME_MAX, b_step_time_target = MOT_STEP_TIME_MAX;

  public:
    bool a_enabled = false;
    bool b_enabled = false;
    bool a_power = false;
    bool b_power = false;
  	uint32_t a_step_time = MOT_STEP_TIME_MAX, b_step_time = MOT_STEP_TIME_MAX;
  
    void init(void);
  	void set_a_enable(bool status);
  	void set_b_enable(bool status);
    bool get_a_enabled(void);
    bool get_b_enabled(void);  	
  	void set_a_power(bool status);
  	void set_b_power(bool status);
    bool get_a_power(void);
    bool get_b_power(void);
    void set_a_dir(bool status);
    void set_b_dir(bool status);
  	void check_step_time_a(void);
  	void check_step_time_b(void);
    void set_a_steptime(uint32_t steptime);
    void set_b_steptime(uint32_t steptime);
    void set_a_rpm(uint32_t rpm);
    void set_b_rpm(uint32_t rpm);
    uint32_t get_a_rpm(void);
    uint32_t get_b_rpm(void);
	
};

#endif

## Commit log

2023-06-26 New version of Python scripts for the RaspiCar
    Python scripts for teh RaspiCar reworked
    [raspicar.py, raspicar_ioctrl.py, raspicar_motors.py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]
2023-06-27 Update raspicar_socket.py
    Bug fix at latency measurement
    [raspicar_socket.py]
2023-07-15 Interface Board with KiCAD added
    [RasPi-Car-B_Cu.gbr, RasPi-Car-B_Mask.gbr, RasPi-Car-B_Paste.gbr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]
2023-07-15 Bug fix
    [RasPi-Car-B_Cu.gbr, RasPi-Car-B_Mask.gbr, RasPi-Car-B_Paste.gbr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]
2023-07-15 Bug fixes
    [RasPi-Car.kicad_pcb, RasPi-Car.kicad_sch]
2023-07-17 Pinout for the interface board added
    [RaspiCar-Raspi-Pinbelegung.ods]
2023-07-17 Interface board pinout added
    [RaspiCar-Raspi-Pinbelegung.ods]
